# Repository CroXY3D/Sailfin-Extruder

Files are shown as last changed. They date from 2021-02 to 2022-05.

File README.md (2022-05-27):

# Sailfin-Extruder
A lightweight compact extruder with 5:1 gearing using BMG dual drive.   It is capable of pushing up to 48mm^3/s through a 0.4 nozzle.

Footprint is a very compact 41x45mm and weighs 107g (with steel fasteners).

Regular and mirrored version.   STEP files provided.  

There also is a version of the middle body which is compatible with toolheads designed for the Sherpa extruder.

Special thanks to Anlin over at Annex Engineering and his Sherpa mini extruder for inspiring the creation of Sailfin.

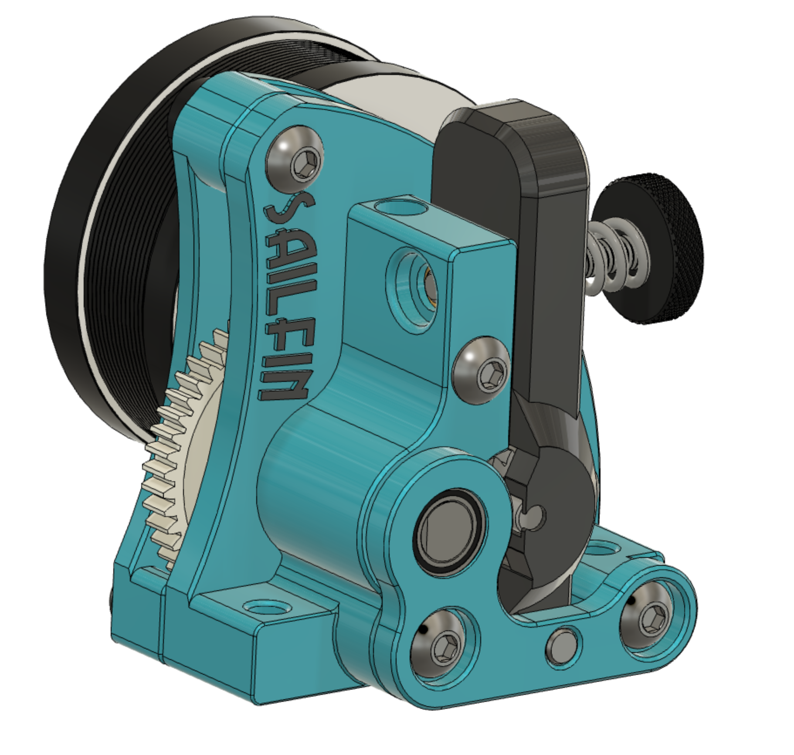
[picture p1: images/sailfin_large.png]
Sailfin


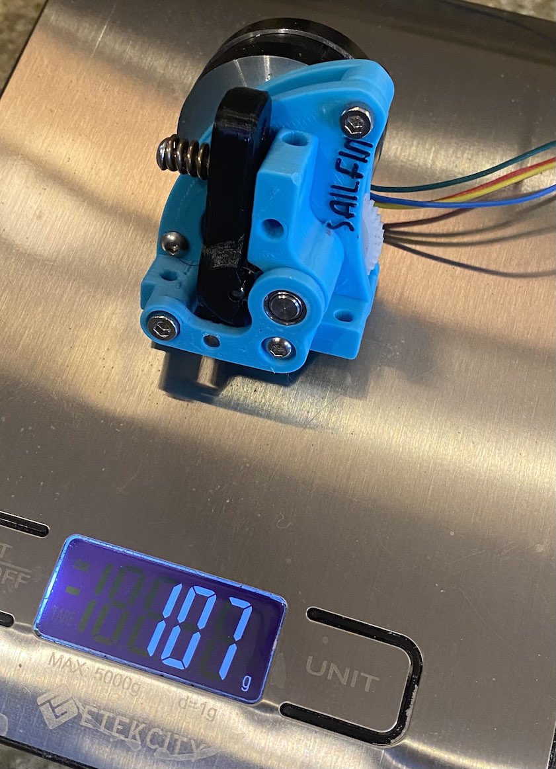
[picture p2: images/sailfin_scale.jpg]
Sailfin Scale


# BOM
* [LDO 17mm Nema14 Stepper with gear LDO-36STH17-1004AHG](https://www.printedsolid.com/products/ldo-nema-14-motor-ldo-36sth17-1004ahg?variant=32690500370517) or 20mm version LDO-36STH20-0504AHG which has more torque.
* [Bondtech BMG or clone internals.  Triangle Lab preferred](https://www.aliexpress.com/item/4000021186440.html)
* 1x M3x25 BHCS (SHCS may be used as well for all BHCS)
* 2x M3x14 BHCS
* 2x M3x10 BHCS
* 5x M3 Heatserts [McMaster](https://www.mcmaster.com/94459A130/) [AliExpress M3xD4.6x4](https://www.aliexpress.com/item/4000232858343.html)
* Short length 2mm ID, 4mm OD PTFE tube.
* Optional [Nema14 heatsink](https://www.filastruder.com/products/heatsink-for-pg35l-geared-stepper-motor?_pos=5&_sid=4f2b94743&_ss=r).  Enables higher motor current and more torque.  The motor is same diam as other 540 size RC motors so there are other heatsinks available from RC shops.
* Optional [Thermal tape for the heatsink](https://smile.amazon.com/Thermal-Adhesive-Performance-Heatsink-Computer/dp/B085CLXM7J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)

# ASSEMBLY
Assembly is fairly straightforward.  

There are two parts with small membranes in holes to make printing a solid bridge.  Drill with 3mm drill bit the membrane on the lever and the membrane on the rear piece.

You may need to either push the white gear down 1-2 mm if it rubs on the Nema 14 motor.  Alternatively you may carefully grind off 1-2mm of the shaft.  Be careful of heat so you don't melt the nylon gear.

The cut guide helper is intended to help you cut the PTFE tube.   Place the PTFE tube in your toolhead and position the cut guide above it.  Use a razor blade to cut the tube.  It's helpful to countersink the top end of the tube with a chamfer bit or a conical deburring tool.

# TOOLHEADS

Toolheads are available for the following:
* Tiny-M V3 Gantry Dragon Toolhead
* Tiny-M V4 Gantry Toolhead (on Tiny-M GitHub)
* Voron V0 Dragon
* Voron V0 V6 Screw Mount

There is a version of the middle body that should be compatible with most Sherpa toolheads.  The motor sits a couple mm lower on the Sailfin, so you may also need a 2mm thick printed spacer to raise the Sailfin.

If you design a toolhead around it, let me know and i'll link or post STLs here.

There will be a Sailfin toolhead for CroXY soon.   

[Nice V0 toolhead that supports Sailfin](https://github.com/KurioHonoo/Mini-AfterSherpa/)

# MODS

[Kayos Maker Mods with some changes for better fitting on Mini-AB](https://github.com/KayosMaker/Sailfin-Extruder)

He also is working on a "Sharkfin" mod.  Poke around his git to find it.

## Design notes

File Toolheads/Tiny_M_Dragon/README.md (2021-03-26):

This is a simple remix of @Xile's remix of the original Tiny-M Toolhead.  This is for the V3 or prior gantry which uses MGN9 for the cross rail.

The Sailfin mount uses the same heatserts that Sailfin uses.

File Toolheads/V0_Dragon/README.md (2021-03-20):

This is a simple remix of @Xile's remix of the original Tiny-M Toolhead.

The Sailfin mount uses the same heatserts that Sailfin uses.

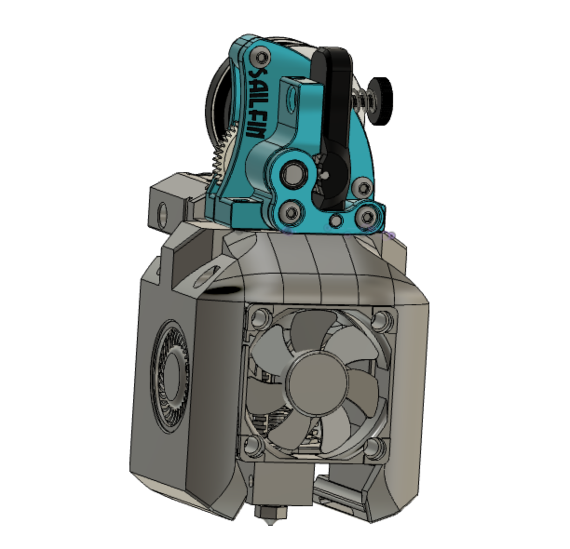
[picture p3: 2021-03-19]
images/tiny_m_dragon.png

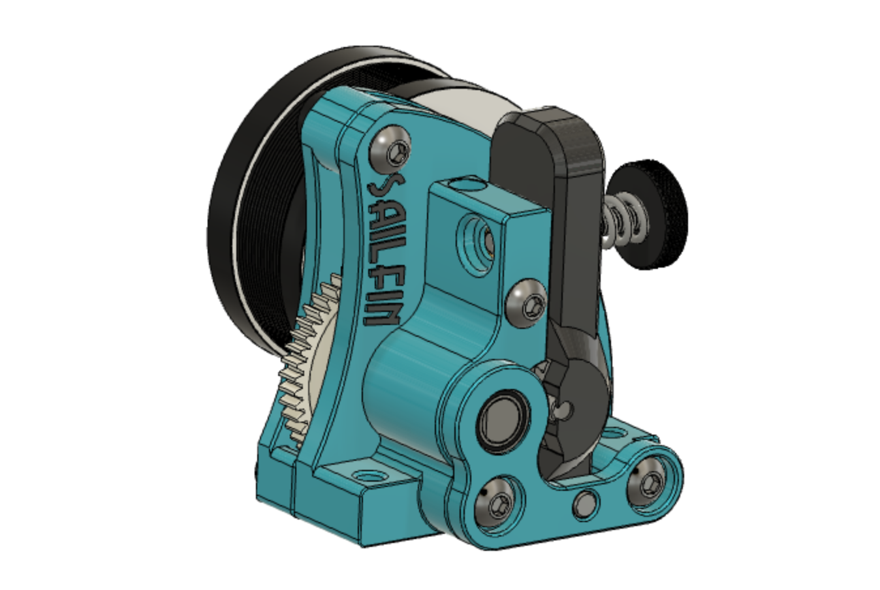
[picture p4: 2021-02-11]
images/sailfin_wide.png

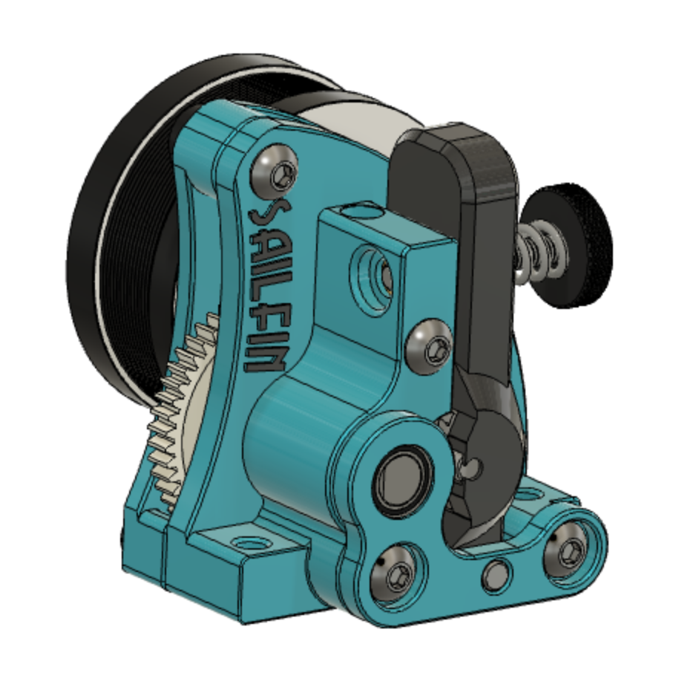
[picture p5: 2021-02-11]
images/sailfin_sm.png

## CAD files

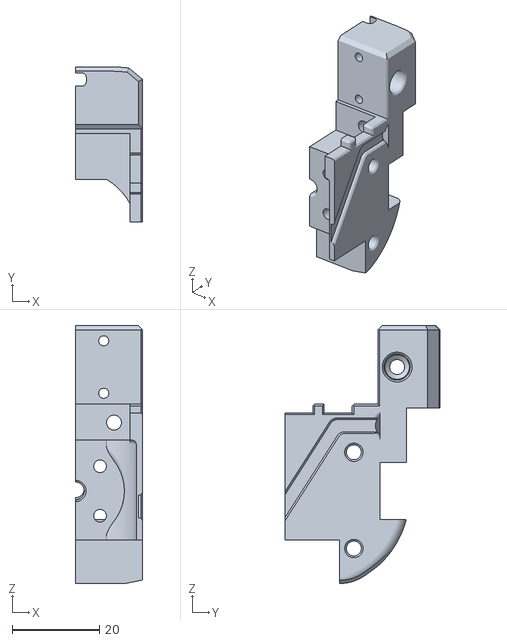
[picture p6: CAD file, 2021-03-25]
Toolheads/V0_Dragon/STL/Toolhead_Dragon_V0_Sailfin_Assembly_Rev2_Toolhead_Assembly v9_Body3_.stl
15.4 x 35.6 x 59.0

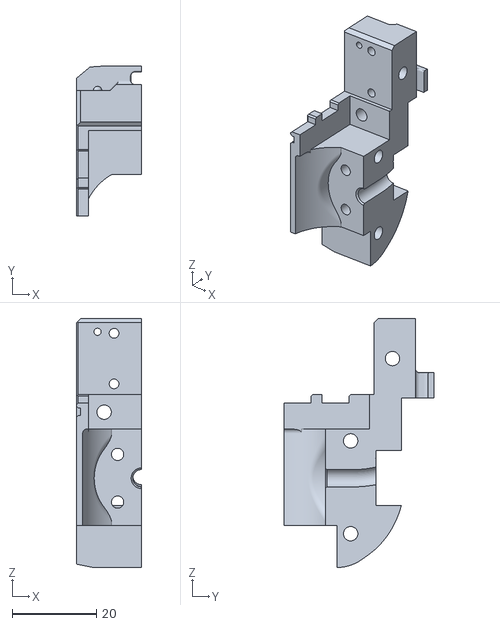
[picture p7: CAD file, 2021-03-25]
Toolheads/V0_Dragon/STL/Toolhead_Dragon_V0_Sailfin_Assembly_Rev2_Toolhead_Assembly v9_Body4_.stl
15.4 x 35.6 x 59.0

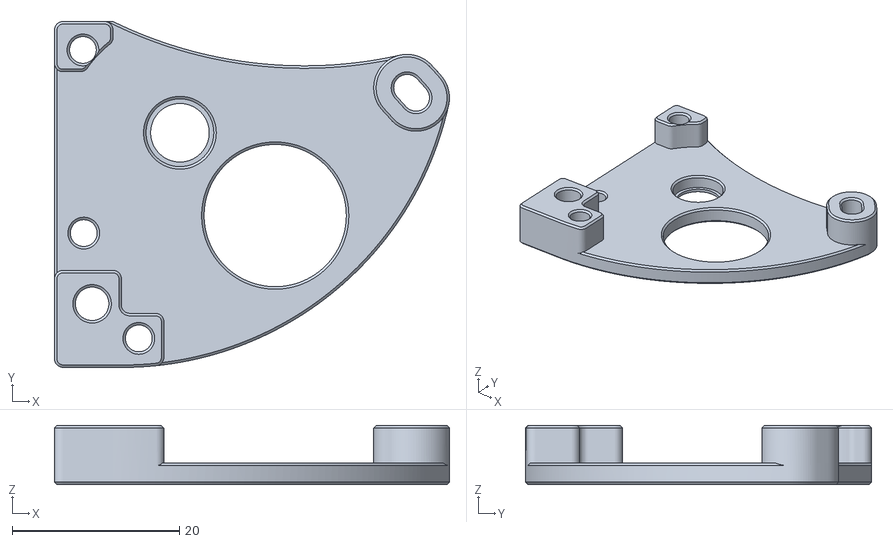
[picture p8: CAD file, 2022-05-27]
STL/Rear.stl
47.2 x 41.4 x 7.07

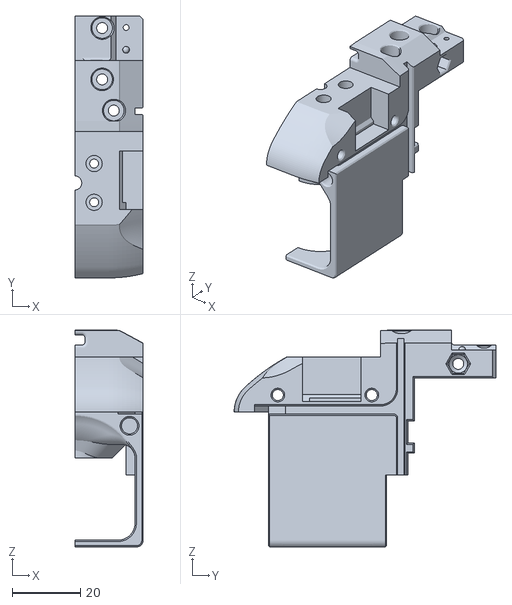
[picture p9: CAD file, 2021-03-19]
Toolheads/Tiny_M_Dragon/STL/duct_right_4.stl
20.0 x 76.5 x 63.4

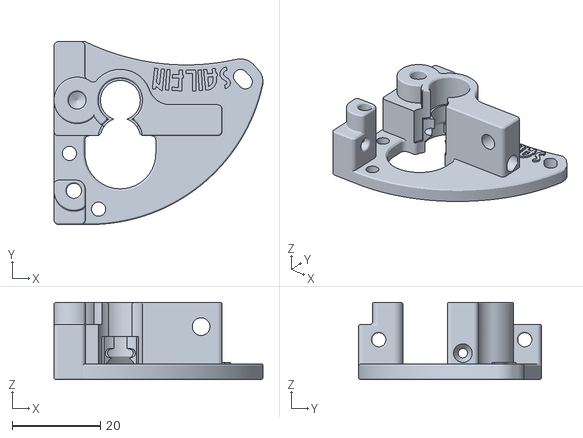
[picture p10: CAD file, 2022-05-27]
STL/Mid.stl
47.2 x 41.4 x 17.5

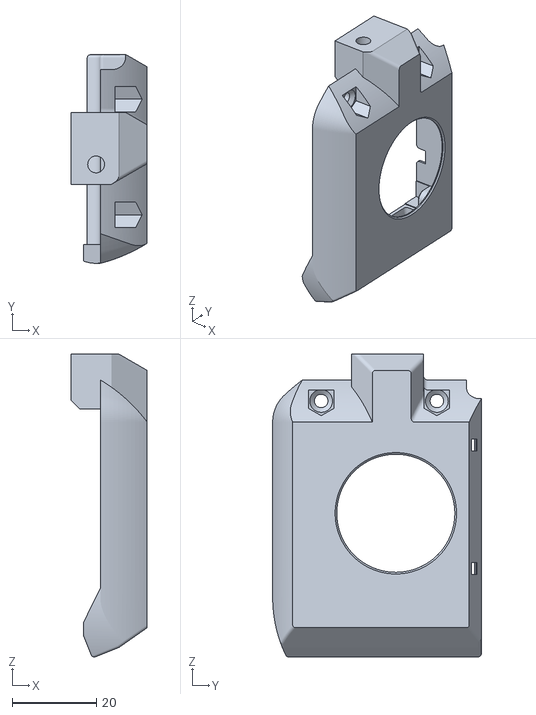
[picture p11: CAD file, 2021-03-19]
Toolheads/Tiny_M_Dragon/STL/duct_right.stl
18.1 x 49.5 x 71.9

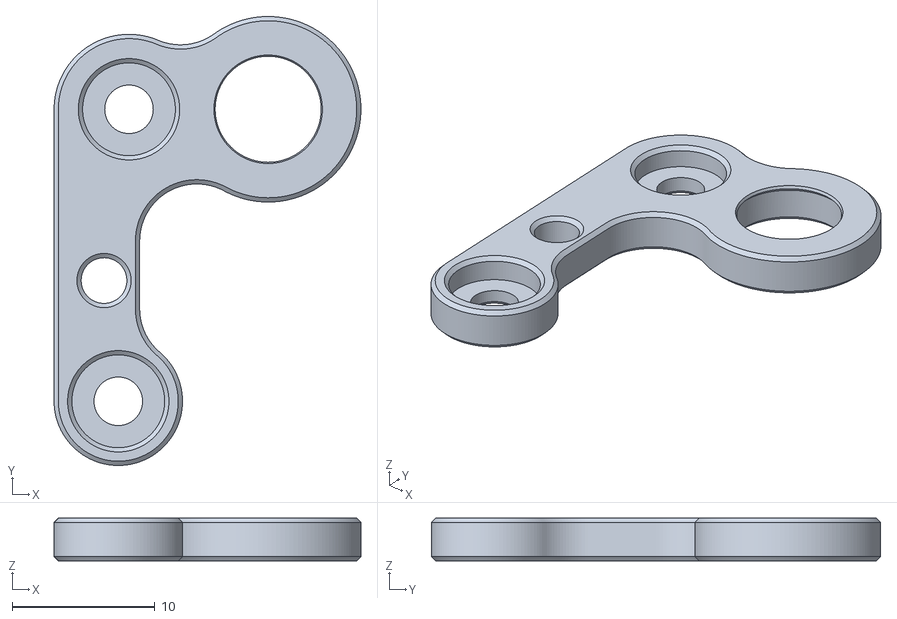
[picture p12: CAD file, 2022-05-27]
STL/Front.stl
21.5 x 31.5 x 3.00

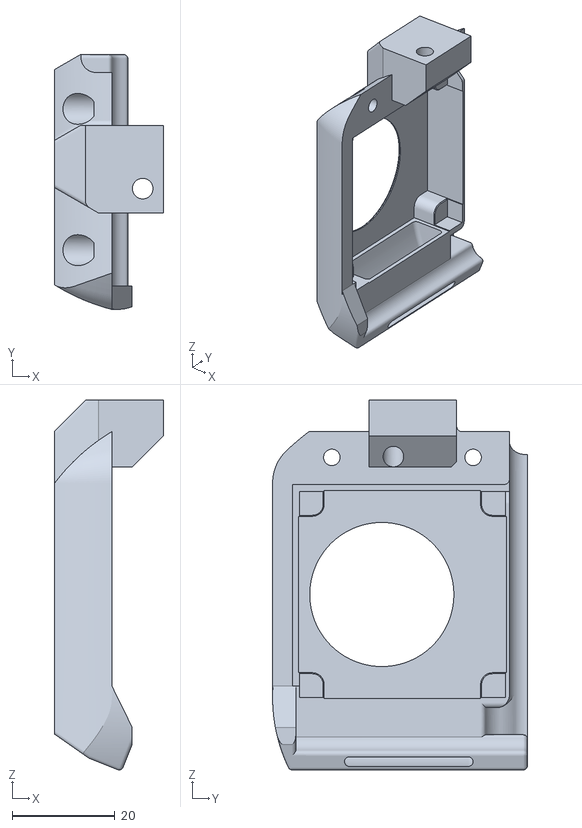
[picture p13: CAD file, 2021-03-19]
Toolheads/Tiny_M_Dragon/STL/duct_right_2.stl
21.1 x 49.5 x 71.9

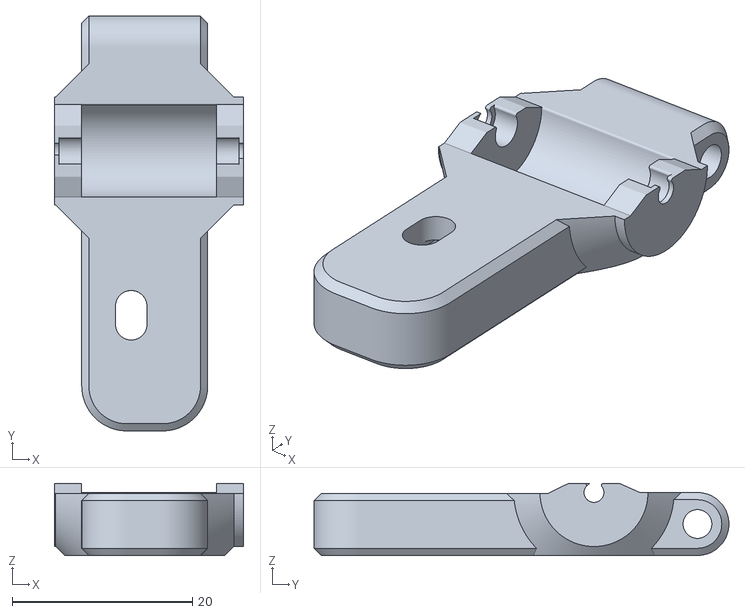
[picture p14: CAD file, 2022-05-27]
STL/Lever.stl
21.0 x 46.1 x 8.00

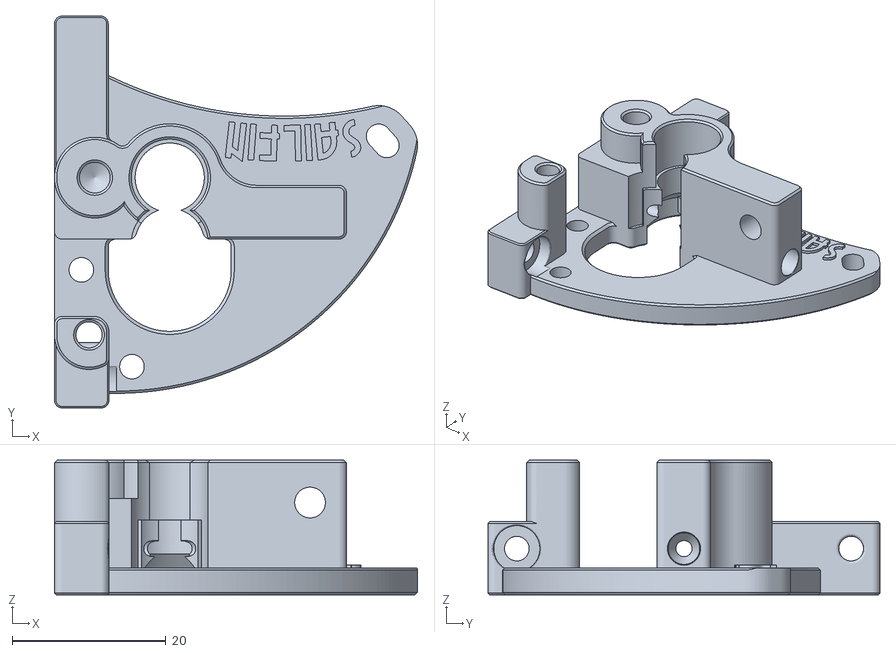
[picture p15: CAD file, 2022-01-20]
STL/Mid_Sherpa_Mount.stl
47.2 x 51.0 x 17.5

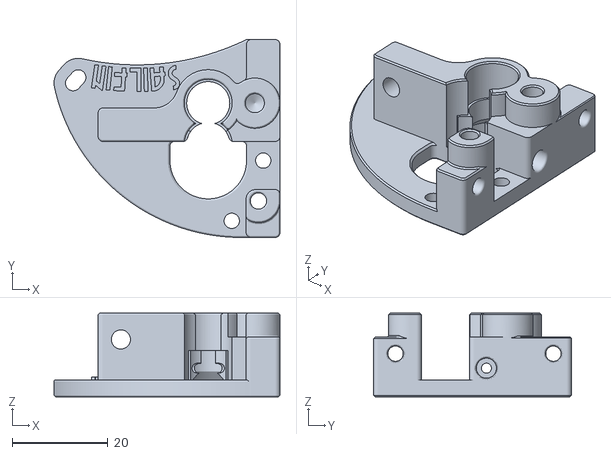
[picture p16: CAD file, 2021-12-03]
STL/Mid_Mirror.stl
47.2 x 41.4 x 17.5

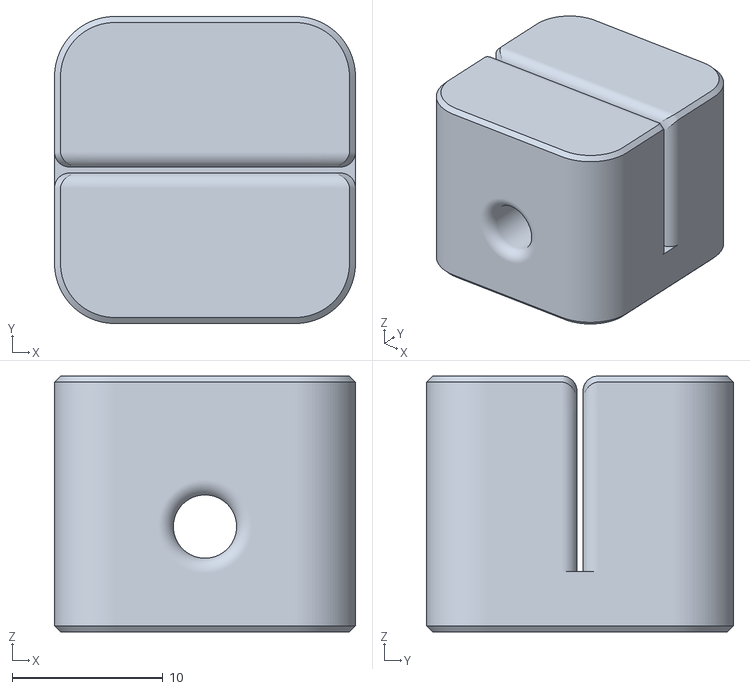
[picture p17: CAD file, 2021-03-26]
STL/Sailfin_PTFE_Cut_Guide.stl
20.0 x 20.4 x 17.0

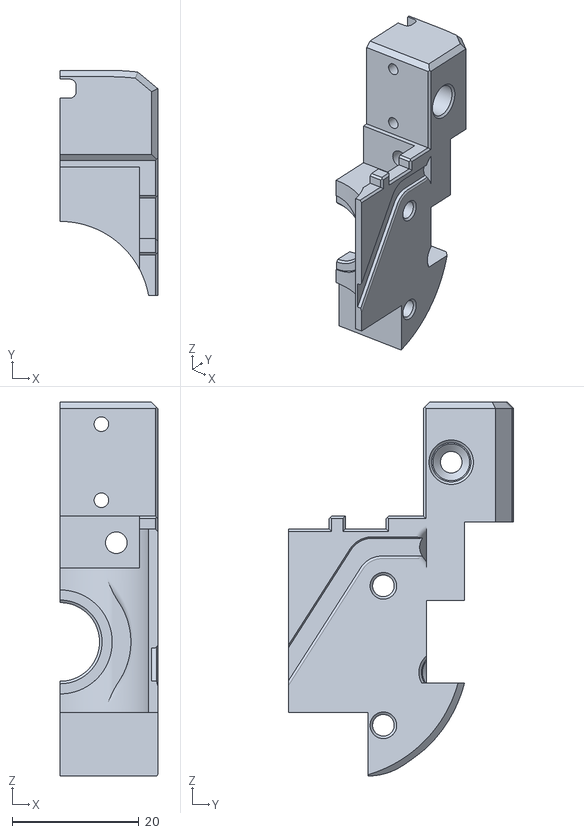
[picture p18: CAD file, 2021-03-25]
Toolheads/V0_V6_Screw_Mount/STL/Toolhead_Threaded_V6_V0_Sailfin_Assembly_Rev2_Toolhead_Assembly v9_Body3_.stl
15.4 x 35.6 x 59.0

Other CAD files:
Toolheads/Tiny_M_Dragon/STL/duct_right_3.stl
STL/Mid_Sherpa_Mount_Mirror.stl
STL/Rear_Mirror.stl
STL/Lever_Mirror.stl
STL/Front_Mirror.stl
Toolheads/V0_V6_Screw_Mount/STL/Toolhead_Threaded_V6_V0_Sailfin_Assembly_Rev2_Toolhead_Assembly v9_Body4_.stl

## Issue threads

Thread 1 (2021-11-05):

heat set inserts

rob911sc, 2021-11-05:
There is no guide or pictures on where the heat set inserts go.

KurioHonoo, 2021-11-05:
It also does not specify the heatset insert size used. If you are coming from the land of Voron then you're likely going to have heatsets that are larger than what the Sailfin was designed for. I believe 4.7mm are used, could be wrong.

bob-u, 2021-12-25:
This extruder design works great and assembly was easy.  Basically all blind holes need inserts.  You can download STEP file from here and open it with STEP viewer to see the assembly.  The inserts are 4.6mm, as I had 4.1...I glued mine :)

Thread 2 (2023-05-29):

Reverse insert gear

jschnarr, 2023-05-29:
The reverse insert BMG gear improves accuracy. Would it be possible to add support to Sailfin?

https://www.bondtech.se/product/bmg-reverse-set-for-hextrudort/

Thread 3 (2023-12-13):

filament sensor orbiter

elpilla, 2023-12-13:
First of all thank you for this fabulous extruder, talking to the modder who created the modification I told him that it would be great if you could put the filament sensor of the orbiter in it and he has created the following modification for the mirror version (it is the one used by the KP3S mod) I leave the link in case it is of interest.
https://www.printables.com/model/282299-sailfin-extruderremix
Again, thank you for this fabulous extruder

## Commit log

2021-03-17 Minor interference fix
    [Front-L.stp, Front-R.stp, Front.stl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]
2021-03-19 tiny m toolhead
    [duct_right.stl, duct_right_2.stl, duct_right_3.stl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]
2021-03-22 Rear Screw no longer protrudes
    [Front-R.stp, Front.stl, Front_Mirror.stl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]
2021-03-24 make room for 8mm washer on tensioner
    [Front.stl, Front_Mirror.stl, Lever.stl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]
2021-03-25 V0 Toolheads
    [Toolhead_Dragon_V0_Sailfin_Assembly_Rev2_Toolhead_Assembly v8_Body3_.stl, Toolhead_Dragon_V0_Sailfin_Assembly_Rev2_Toolhead_Assembly v8_Body4_.stl, Toolhead_Th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]
2021-03-26 mirroed schlurpa
    [Front_Mirror.stl, Lever_Mirror.stl, Mid_Mirror.stl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]
2021-03-26 fix slurpee mount interference
    [Front.stl, Front_Mirror.stl, Lever.stl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]
2021-03-26 PTFE Cut guide
    [Sailfin_PTFE_Cut_Guide.stl]
2021-03-29 Funky arc be gone
    [Toolhead_Dragon_V0_Sailfin_Assembly_Rev2_Toolhead_Assembly v8_Body3_.stl, Toolhead_Dragon_V0_Sailfin_Assembly_Rev2_Toolhead_Assembly v8_Body4_.stl, Toolhead_Dr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]
2021-04-01 Dropping the C.
    [Mid_Sherpa_Mount.stl, Mid_Sherpa_Mount_Mirror.stl]
2021-05-16 minor bearing seat issues
    [Rear.stl, Rear_Mirror.stl]
2021-12-03 update step. move one screw tiny bit so larger heatserts work
    [Front-R.stl, Front.stl, Lever.stl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]
2022-01-20 Sherpa Mount Minor tweak of residual hole bit
    [Mid_Sherpa_Mount.stl]
